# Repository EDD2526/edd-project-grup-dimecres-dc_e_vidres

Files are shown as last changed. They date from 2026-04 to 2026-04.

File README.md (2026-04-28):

View this project on [CADLAB.io](https://cadlab.io/project/30192). 

# Projecte ALÇA-VIDRES

>**Autors:** Àlex Requena , Alfred Abanto
>**Versió:** v3.2

----------

## Objectiu

>PCB per controlar les portes d'un cotxe.
Control de finestres
Controls de seguretat en finestres
Sistema de tancament i obertura de portes
Obertura de portes amb un lector RFID

## Diagrama de blocs
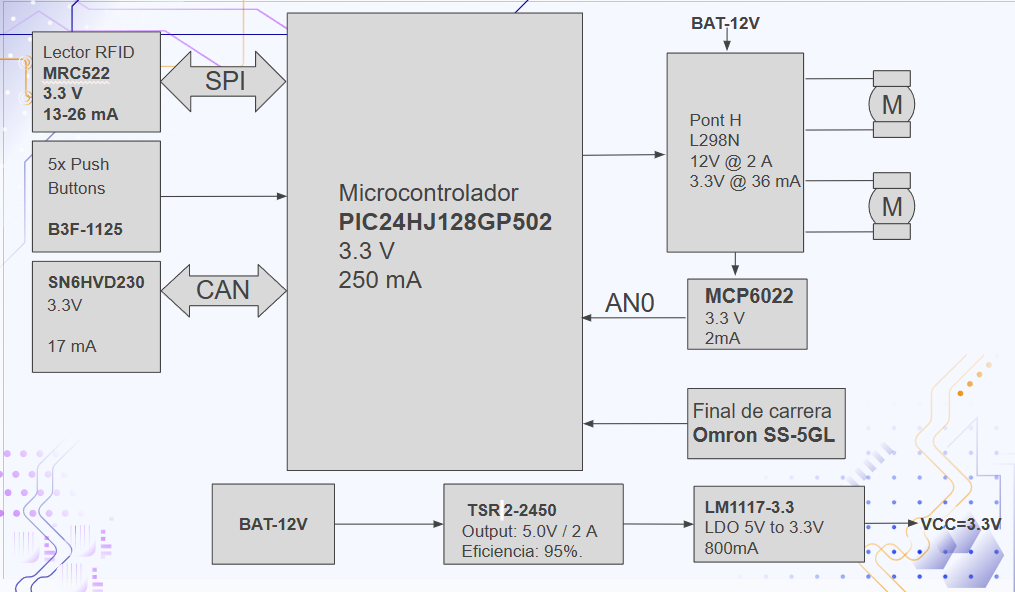
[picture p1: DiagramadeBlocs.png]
DIAGRAMA


### Descripció/funcionalitat de cada bloc
Microcontrolador PIC24HJ: Cervell del sistema; processa dades i coordina tots els mòduls i comunicacions.

Lector RFID MFRC522: Mòdul de comunicació sense contacte per a identificació de targetes via interfície SPI.

Polsadors B3F: Interfície d'usuari per a l'activació manual de funcions del sistema.

Transceptor CAN TJA1051: Interfície de comunicació robusta per a l'enviament de dades a llarga distància.

Pont H L298N: Driver de potència per controlar el gir i la velocitat de dos motors DC.

Amp. Op. MCP6022: Condiciona senyals analògics (com el consum dels motors) per a una lectura precisa del micro.

Final de carrera SS-01GL111-ET: Sensor mecànic de seguretat que detecta el límit de moviment físic.

Conversor TSR 2-2450: Transforma eficientment els 12V de la bateria en 5V estables.

Regulador LM1117-3.3: Redueix els 5V a 3.3V per alimentar la lògica i els xips de control.
## Requisits / Especificacions

----

## Components

| Descripci&#243; | Ref | Package |Datasheet | Prove&#239;dor | Preu | Unitats |
| Driver de Motor (Puente H) | L298N | TO-220-15 | [Datasheet](https://www.alldatasheet.com/datasheet-pdf/view/22440/STMICROELECTRONICS/L298N.html) | [Mouser](https://www.mouser.es/c/?q=L298N) | 10.31 &euro; | 1x |

| Convertidor DC-DC | TSR2-2450 | SIP-3 | https://www.tracopower.com/products/tsr2.pdf | https://www.mouser.es/c/?q=TSR2-2450 | 10.41 € | 1x |

| Amplificador Op. | MCP6022 | SOIC-8 | [Datasheet](https://www.alldatasheet.com/datasheet-pdf/view/99099/MICROCHIP/MCP6022.html) | [Mouser](https://www.mouser.es/c/?q=MCP6022) | 1.53 &euro; | 1x |
-----------
| Regulador LDO | LM1117DT-3.3 | TO-252 | https://www.ti.com/lit/ds/symlink/lm1117.pdf | https://www.mouser.es/c/?q=LM1117DT-3.3 | 1.5 € | 1x |
| Lector RFID | MFRC52201HN1_157 | HVQFN-32 | https://www.nxp.com/docs/en/data-sheet/MFRC522.pdf | https://www.mouser.es/c/?q=MFRC52201HN1_157 | 6.8€ | 1x |

| Microcontrolador | PIC24HJ64GP504-I/PT | TQFP-44 | https://ww1.microchip.com/downloads/en/DeviceDoc/70293G.pdf | https://www.mouser.es/c/?q=PIC24HJ64GP504-I/PT | 5.75 € | 1x |

| Transceptor CAN | SN65HVD230 | SOIC-8 | https://www.ti.com/lit/ds/symlink/sn65hvd230.pdf | https://www.mouser.es/c/?q=SN65HVD230 | 1.91 € | 1x |

| Ferrita | FerriteBead | SMD 0805 | https://www.vishay.com/docs/34025/ilbb0805.pdf| [Mouser](https://www.mouser.es/c/?q=Ferrite%20Bead%200805) | 0.08 &euro; | 1x |

| Conector D-Sub 9 | A-DF 09 LL/Z | THT | https://www.assmann-wsw.com/fileadmin/datasheets/ASS_0212_CO.pdf | https://www.mouser.es/c/?q=A-DF+09+LL%2FZ | 2.18 € | 2x |
## Software
Kicad
### Eines:

  * KiCad 10.0 

### Funcionalitats:
Controlar finestres.

Controls de seguretat en finestres.

Sistema de tancament i obertura de portes.

Obrir portes amb un lector RFID.

-----------

## Historial de canvis
|11/03| Alfred | Main | v0.0 | Diagrama de blocs i 
components |
|18/03| Àlex | Main | v0.1 | Esquemàtic i simulacions |
| 25/03| Àlex | Main | v1 | layoutv1|
| 10/04| Alfred | Main | v2 | layoutv2, dues etapes|
| 10/04| Alfred | Main | v3.0 | layoutv2, redistribució|
| 22/04| Àlex | Main | v3.1 | layoutv3, errors arreglats|
| 27/04| Àlex i Alfred | Main | v3.2| layoutv3, layout final|

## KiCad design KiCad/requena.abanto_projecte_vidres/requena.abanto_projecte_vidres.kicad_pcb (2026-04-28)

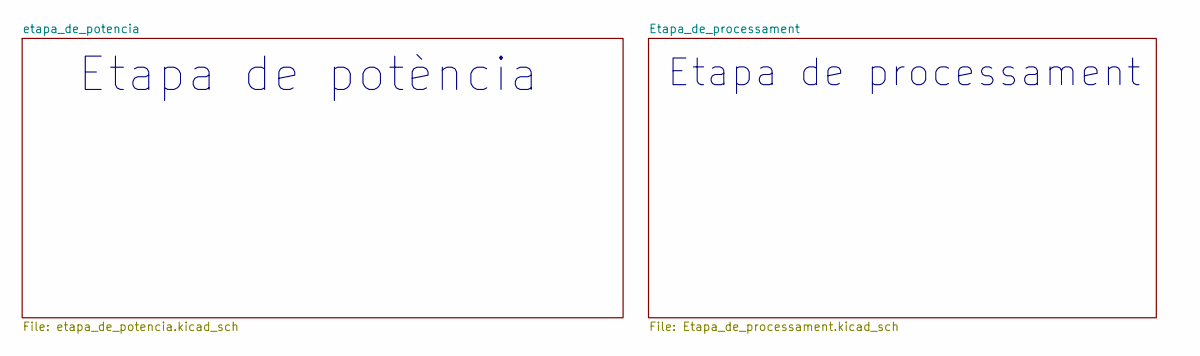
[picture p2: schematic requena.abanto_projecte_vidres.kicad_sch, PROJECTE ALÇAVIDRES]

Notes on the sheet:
Etapa de processament
Etapa de potència

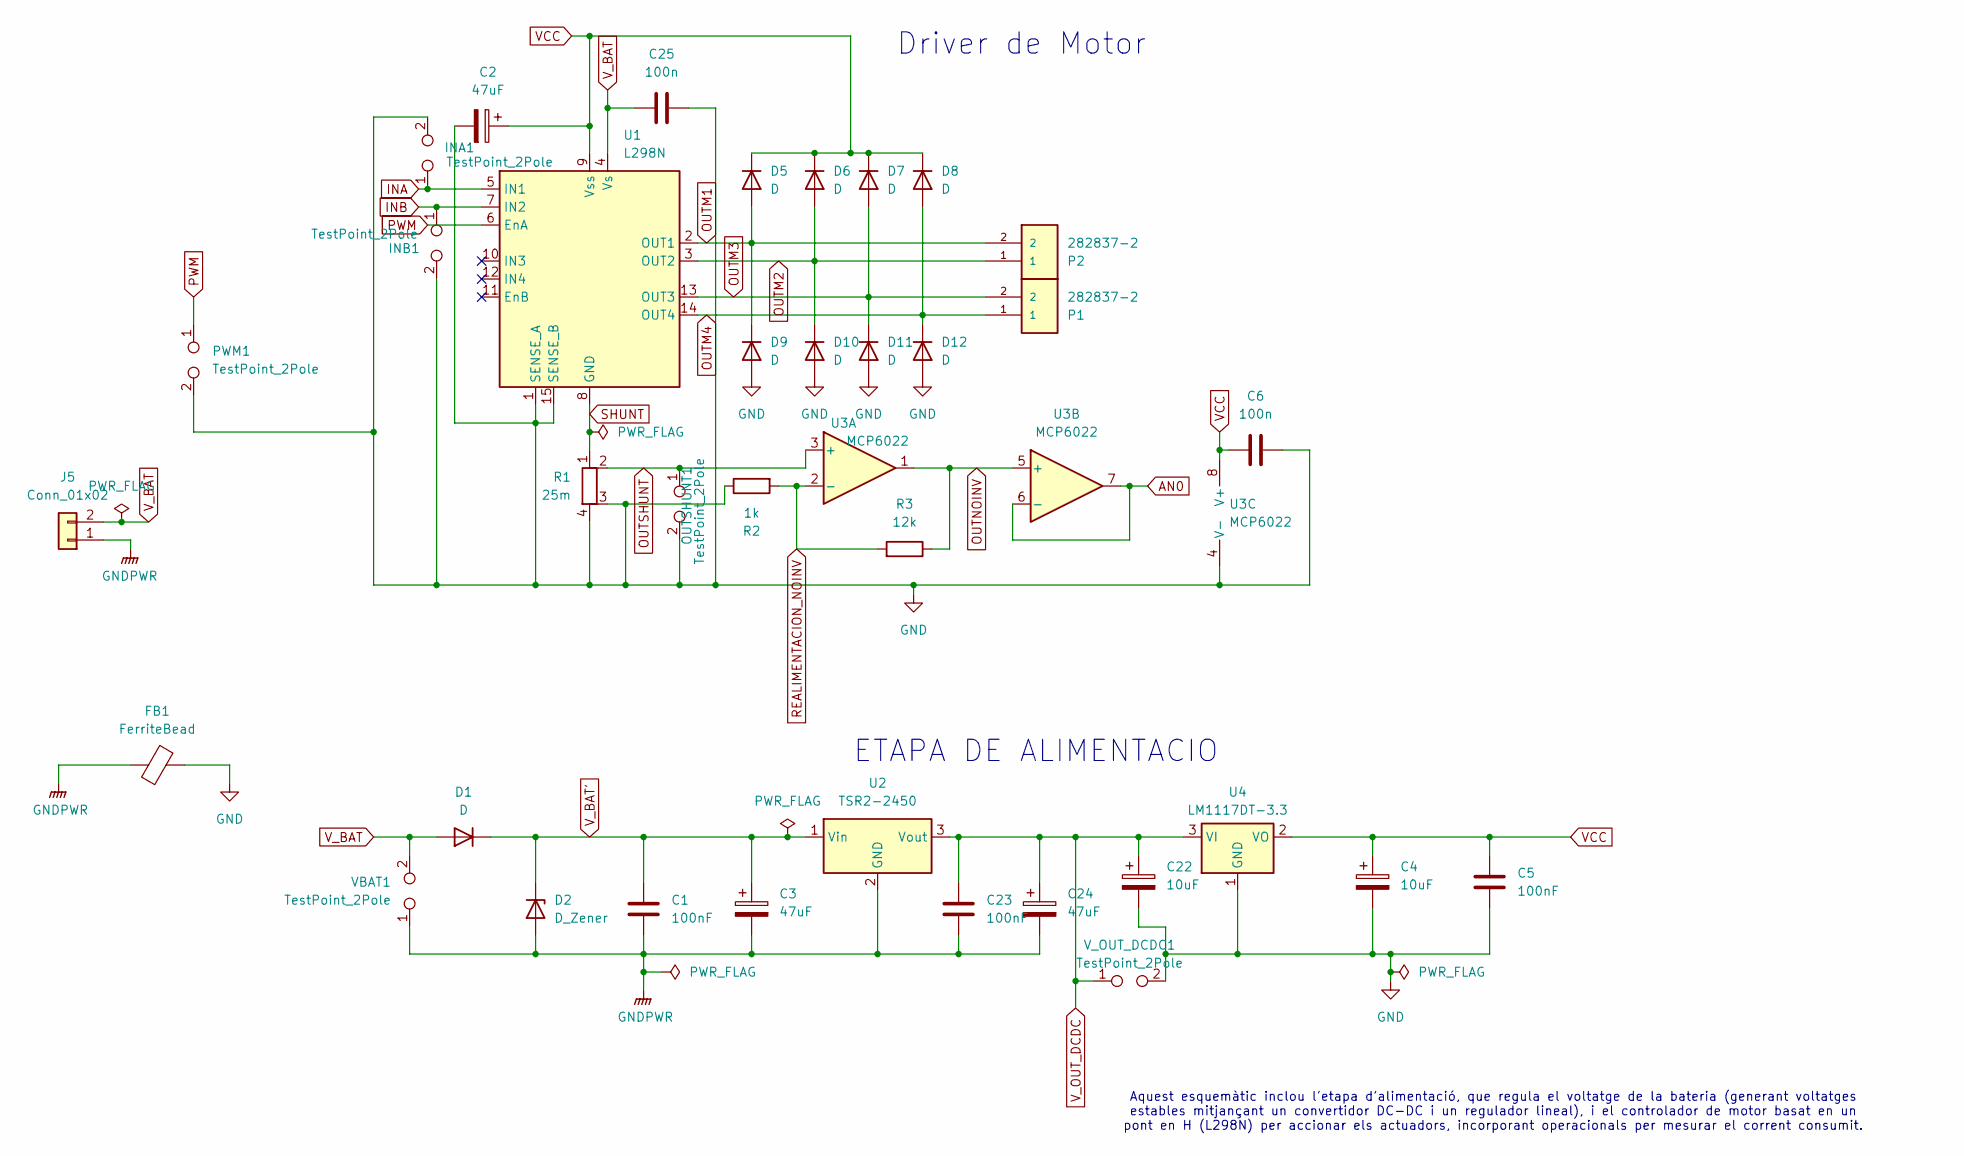
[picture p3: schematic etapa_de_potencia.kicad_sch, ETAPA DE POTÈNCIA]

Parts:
C1, C5, C23: 100nF; C_0805_2012Metric
C2, C3, C24: 47uF; CP_Radial_D4.0mm_P1.50mm
C4, C22: 10uF; CP_Radial_D4.0mm_P1.50mm
C6, C25: 100n; C_0603_1608Metric
D1: D; D_DO-41_SOD81_P12.70mm_Horizontal
D2: D_Zener; D_A-405_P2.54mm_Vertical_AnodeUp
D5, D6, D7, D8, D9, D10, D11, D12: D; D_DO-201AD_P15.24mm_Horizontal
FB1: FerriteBead; L_0805_2012Metric
INA1: TestPoint_2Pole; TestPoint_2Pads_Pitch2.54mm_Drill0.8mm
INB1: TestPoint_2Pole; TestPoint_2Pads_Pitch2.54mm_Drill0.8mm
J5: Conn_01x02; TerminalBlock_Xinya_XY308-2.54-2P_1x02_P2.54mm_Horizontal
OUTSHUNT1: TestPoint_2Pole; TestPoint_2Pads_Pitch2.54mm_Drill0.8mm
P1, P2: 282837-2; TE_282837-2; PARTREV G3
PWM1: TestPoint_2Pole; TestPoint_2Pads_Pitch2.54mm_Drill0.8mm
R1: 25m; R_Shunt_Vishay_WSK2512_6332Metric_T1.19mm
R2: 1k; R_1206_3216Metric
R3: 12k; R_1206_3216Metric
U1: L298N; TO-220-15_P2.54x5.08mm_StaggerOdd_Lead4.58mm_Vertical
U2: TSR2-2450; Converter_DCDC_TRACO_TSR2-xxxx_THT
U3: MCP6022; SOIC-8_3.9x4.9mm_P1.27mm
U4: LM1117DT-3.3; TO-252-2
VBAT1: TestPoint_2Pole; TestPoint_2Pads_Pitch2.54mm_Drill0.8mm
V_OUT_DCDC1: TestPoint_2Pole; TestPoint_2Pads_Pitch2.54mm_Drill0.8mm

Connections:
AN0: U3.6 (-), U3.7; also elsewhere on the board
GNDPWR: C1.2, C3.2, C23.2, C24.2, D2.2 (A), FB1.1, J5.1, U2.2 (GND), VBAT1.1
INA: INA1.1, U1.5 (IN1); also elsewhere on the board
INB: INB1.1, U1.7 (IN2); also elsewhere on the board
OUTM1: D5.2 (A), D9.1 (K), P2.2, U1.2 (OUT1)
OUTM2: D6.2 (A), D10.1 (K), P2.1, U1.3 (OUT2)
OUTM3: D7.2 (A), D11.1 (K), P1.2, U1.13 (OUT3)
OUTM4: D8.2 (A), D12.1 (K), P1.1, U1.14 (OUT4)
OUTNOINV: R3.1, U3.1, U3.5 (+)
OUTSHUNT: OUTSHUNT1.1, R1.2, U3.3 (+)
PWM: PWM1.1, U1.6 (EnA); also elsewhere on the board
REALIMENTACION_NOINV: R2.2, R3.2, U3.2 (-)
SHUNT: R1.1, U1.8 (GND)
VCC: C2.1, C4.1, C5.1, C6.1, D5.1 (K), D6.1 (K), D7.1 (K), D8.1 (K), U1.9 (Vss), U3.8 (V+), U4.2 (VO); also elsewhere on the board
V_BAT: C25.1, D1.2 (A), J5.2, U1.4 (Vs), VBAT1.2
V_BAT': C1.1, C3.1, D1.1 (K), D2.1 (K), U2.1 (Vin)
V_OUT_DCDC: C22.1, C23.1, C24.1, U2.3 (Vout), U4.3 (VI), V_OUT_DCDC1.1

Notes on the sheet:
Aquest esquemàtic inclou l'etapa d'alimentació, que regula el voltatge de la bateria (generant voltatges estables mitjançant un convertidor DC-DC i un regulador lineal), i el controlador de motor basat en un pont en H (L298N) per accionar els actuadors, incorporant operacionals per mesurar el corre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
Driver de Motor
ETAPA DE ALIMENTACIO

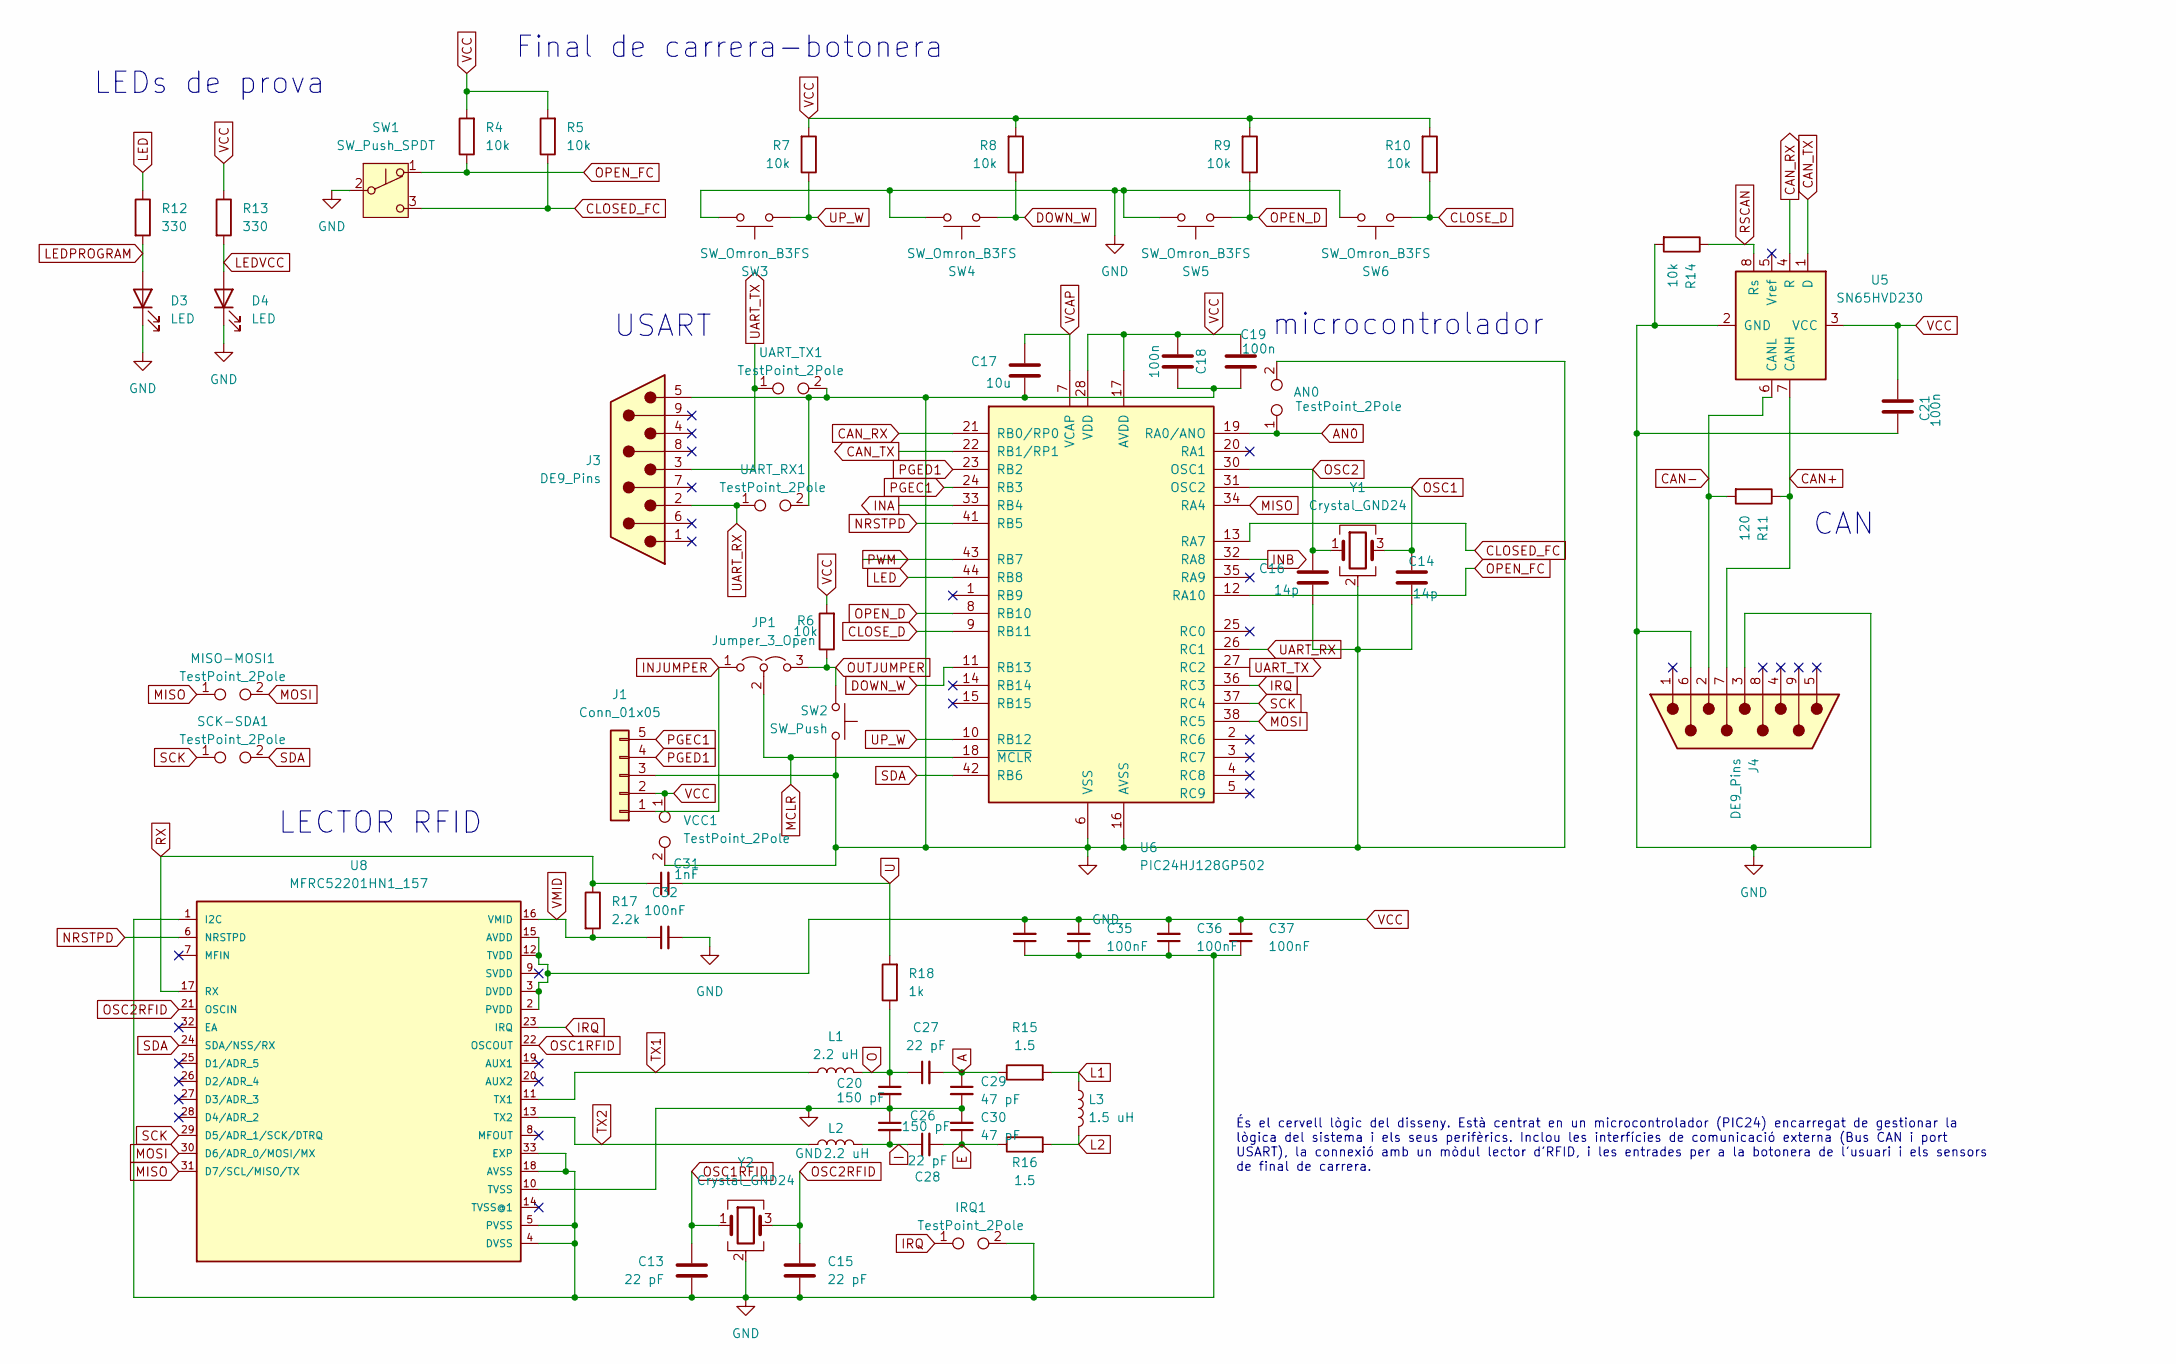
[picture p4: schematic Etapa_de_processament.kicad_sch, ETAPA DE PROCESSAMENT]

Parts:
AN0: TestPoint_2Pole; TestPoint_2Pads_Pitch2.54mm_Drill0.8mm
C13, C15: 22 pF; C_0805_2012Metric
C14, C16: 14p; C_0805_2012Metric
C17: 10u; C_0603_1608Metric
C18, C19, C21: 100n; C_0603_1608Metric
C20, C26: 150 pF; C_1206_3216Metric
C27, C28: 22 pF; C_1206_3216Metric
C29, C30: 47 pF; C_1206_3216Metric
C31: 1nF; C_1206_3216Metric
C32: 100nF; C_1206_3216Metric
C34, C35, C36, C37: 100nF; C_0603_1608Metric
D3, D4: LED; D_0805_2012Metric
IRQ1: TestPoint_2Pole; TestPoint_2Pads_Pitch2.54mm_Drill0.8mm
J1: Conn_01x05; PinHeader_1x05_P2.54mm_Vertical
J3, J4: DE9_Pins; DSUB-9_Pins_Horizontal_P2.77x2.54mm_EdgePinOffset9.40mm
JP1: Jumper_3_Open; PinHeader_1x03_P2.54mm_Vertical
L1, L2: 2.2 uH; L_1206_3216Metric
L3: 1.5 uH; L_1206_3216Metric
MISO-MOSI1: TestPoint_2Pole; TestPoint_2Pads_Pitch2.54mm_Drill0.8mm
R4, R5, R6, R7, R8, R9, R10, R14: 10k; R_1206_3216Metric
R11: 120; R_1206_3216Metric
R12, R13: 330; R_1206_3216Metric
R15, R16: 1.5; R_1206_3216Metric
R17: 2.2k; R_1206_3216Metric
R18: 1k; R_1206_3216Metric
SCK-SDA1: TestPoint_2Pole; TestPoint_2Pads_Pitch2.54mm_Drill0.8mm
SW1: SW_Push_SPDT; SW_SPDT_PCM12
SW2: SW_Push; SW_SPST_Omron_B3FS-100xP
SW3, SW4, SW5, SW6: SW_Omron_B3FS; SW_SPST_Omron_B3FS-100xP
U5: SN65HVD230; SOIC-8_3.9x4.9mm_P1.27mm
U6: PIC24HJ128GP502; TQFP-44_10x10mm_P0.8mm
U8: MFRC52201HN1_157; QFN50P500X500X100-33N
UART_RX1: TestPoint_2Pole; TestPoint_2Pads_Pitch2.54mm_Drill0.8mm
UART_TX1: TestPoint_2Pole; TestPoint_2Pads_Pitch2.54mm_Drill0.8mm
VCC1: TestPoint_2Pole; TestPoint_2Pads_Pitch2.54mm_Drill0.8mm
Y1: Crystal_GND24; Crystal_SMD_3225-4Pin_3.2x2.5mm
Y2: Crystal_GND24; Crystal_SMD_2520-4Pin_2.5x2.0mm

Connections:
A: C27.2, C29.1, R15.1
AN0: AN0.1, U6.19 (RA0/ANO); also elsewhere on the board
CAN+: J4.7, R11.1, U5.7 (CANH)
CAN-: J4.2, R11.2, U5.6 (CANL)
CAN_RX: U5.4 (R), U6.21 (RB0/RP0)
CAN_TX: U5.1 (D), U6.22 (RB1/RP1)
CLOSED_FC: R5.1, SW1.3 (C), U6.13 (RA7)
CLOSE_D: R10.1, U6.9 (RB11); also elsewhere on the board
DOWN_W: R8.1, U6.11 (RB13); also elsewhere on the board
E: C28.2, C30.1, R16.1
I: C26.2, C28.1, L2.2
INA: U6.33 (RB4); also elsewhere on the board
INB: U6.32 (RA8); also elsewhere on the board
INJUMPER: J1.1, JP1.1 (A)
IRQ: IRQ1.1, U6.36 (RC3), U8.23 (IRQ)
L1: L3.1, R15.2
L2: L3.2, R16.2
LED: R12.1, U6.44 (RB8)
LEDPROGRAM: D3.2 (A), R12.2
LEDVCC: D4.2 (A), R13.2
MCLR: JP1.2 (C), U6.18 (~MCLR)
MISO: MISO-MOSI1.1, U6.34 (RA4), U8.31 (D7/SCL/MISO/TX)
MOSI: MISO-MOSI1.2, U6.38 (RC5), U8.30 (D6/ADR_0/MOSI/MX)
NRSTPD: U6.41 (RB5), U8.6 (NRSTPD)
O: C20.1, C27.1, L1.2, R18.1
OPEN_D: R9.1, U6.8 (RB10); also elsewhere on the board
OSC1: C14.1, U6.31 (OSC2), Y1.3
OSC1RFID: C13.1, U8.22 (OSCOUT), Y2.1
OSC2: C16.1, U6.30 (OSC1), Y1.1
OSC2RFID: C15.1, U8.21 (OSCIN), Y2.3
OUTJUMPER: JP1.3 (B), R6.1; also elsewhere on the board
PGEC1: J1.5, U6.24 (RB3)
PGED1: J1.4, U6.23 (RB2)
PWM: U6.43 (RB7); also elsewhere on the board
RSCAN: R14.1, U5.8 (Rs)
RX: C31.1, R17.1, U8.17 (RX)
SCK: SCK-SDA1.1, U6.37 (RC4), U8.29 (D5/ADR_1/SCK/DTRQ)
SDA: SCK-SDA1.2, U6.42 (RB6), U8.24 (SDA/NSS/RX)
TX1: L1.1, U8.11 (TX1)
TX2: L2.1, U8.13 (TX2)
U: C31.2, R18.2
UART_RX: J3.2, U6.26 (RC1), UART_RX1.1
UART_TX: J3.3, U6.27 (RC2), UART_TX1.1
VCAP: C17.1, U6.7 (VCAP)
VCC: C18.2, C19.1, C21.1, C34.2, C35.2, C36.2, C37.2, J1.2, R4.2, R5.2, R6.2, R7.2, R8.2, R9.2, R10.2, R13.1, U5.3 (VCC), U6.17 (AVDD), U6.28 (VDD), U6.40 (VDD), U8.2 (PVDD), U8.3 (DVDD), U8.12 (TVDD), U8.15 (AVDD), VCC1.1; also elsewhere on the board
VMID: C32.1, R17.2, U8.16 (VMID)

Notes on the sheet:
CAN
LEDs de prova
LECTOR RFID
microcontrolador
USART
Final de carrera-botonera
És el cervell lògic del disseny. Està centrat en un microcontrolador (PIC24) encarregat de gestionar la lògica del sistema i els seus perifèrics. Inclou les interfícies de comunicació externa (Bus CAN i port USART), la connexió amb un mòdul lector d'RFID, i les entrades per a la botonera de l'usuar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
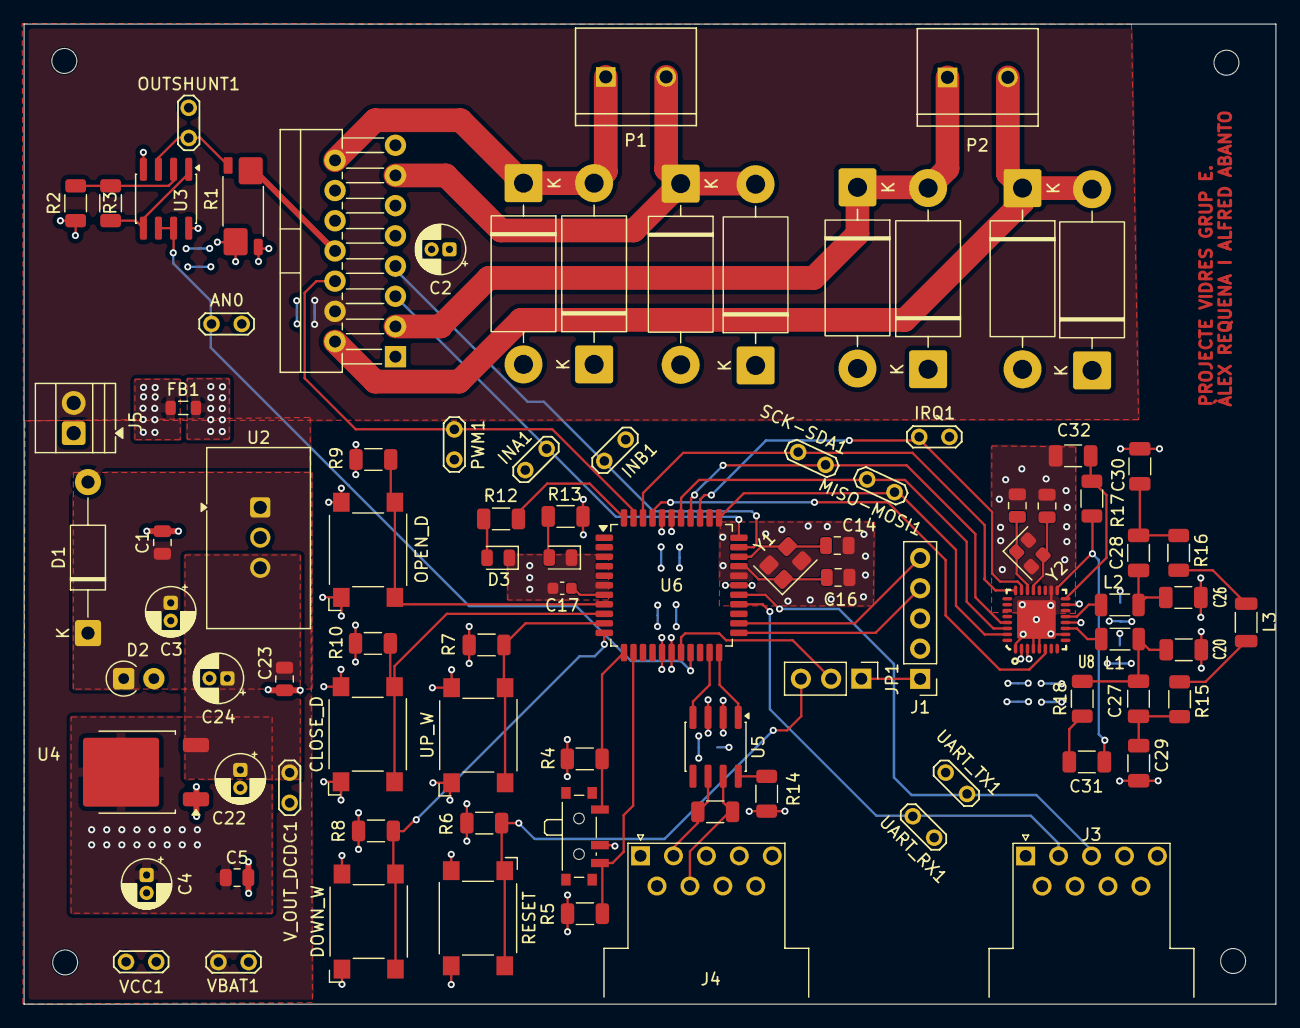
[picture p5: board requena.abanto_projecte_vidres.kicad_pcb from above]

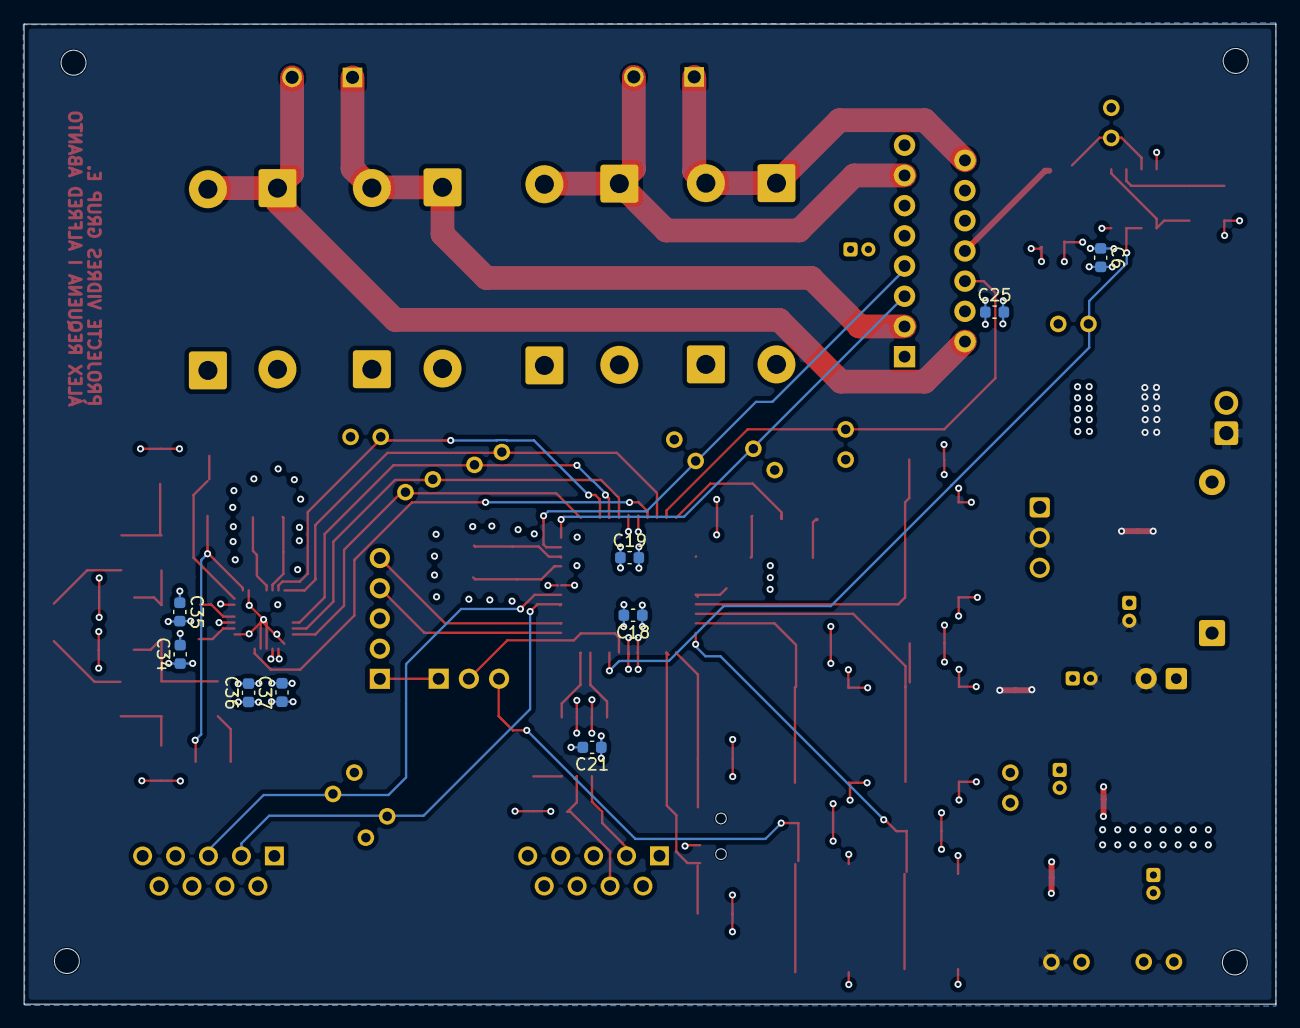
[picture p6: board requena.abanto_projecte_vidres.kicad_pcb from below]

Board: 4 copper layers, 105.3 x 82.4 mm, 99 parts (9 on the bottom side), 61 nets.

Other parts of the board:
CLOSE_D: SW_Omron_B3FS; SW_SPST_Omron_B3FS-100xP
DOWN_W: SW_Omron_B3FS; SW_SPST_Omron_B3FS-100xP
OPEN_D: SW_Omron_B3FS; SW_SPST_Omron_B3FS-100xP
RESET: SW_Push; SW_SPST_Omron_B3FS-100xP
UP_W: SW_Omron_B3FS; SW_SPST_Omron_B3FS-100xP

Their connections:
CLOSE_D: CLOSE_D.2; also elsewhere on the board
DOWN_W: DOWN_W.2; also elsewhere on the board
OPEN_D: OPEN_D.2; also elsewhere on the board
OUTJUMPER: RESET.1; also elsewhere on the board

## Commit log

2026-03-11 creacion proyecto kikad
    [requena.abanto_projecte_vidres.kicad_pcb, requena.abanto_projecte_vidres.kicad_sch]
2026-03-12 Creacio d'etapes
    [Etapa_de_alimentacio.kicad_sch, Etapa_de_comunicacio.kicad_sch, Etapa_de_processament.kicad_sch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]
2026-03-14 etapa alimentación empezada
    [Etapa_de_alimentacio.kicad_sch]
2026-03-15 avance can
    [Etapa_de_comunicacio.kicad_sch]
2026-03-15 avance etapa-de-processament
    [Etapa_de_processament.kicad_sch]
2026-03-15 He ficar un led
    [Etapa_de_processament.kicad_sch]
2026-03-15 avance comunicaciones
    [Etapa_de_comunicacio.kicad_sch]
2026-03-15 posar etiquetes
    [Etapa_de_processament.kicad_sch]
2026-03-15 millora circuit
    [Etapa_de_processament.kicad_sch]
2026-03-15 proteccion alimentacion
    [Etapa_de_alimentacio.kicad_sch]
2026-03-15 avance sensores
    [Etapa_de_sensors.kicad_sch]
2026-03-15 avance etapa de potencia
    [etapa_de_potencia.kicad_sch]
2026-03-16 cambios de clase
    [Etapa_de_processament.kicad_sch, Etapa_de_sensors.kicad_sch]
2026-03-16 arreglos :)
    [Etapa_de_comunicacio.kicad_sch]
2026-03-17 millora el esquematic
    [Etapa_de_comunicacio.kicad_sch, Etapa_de_processament.kicad_sch, Etapa_de_sensors.kicad_sch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]
2026-03-22 Millora projecte 1
    [Etapa_de_alimentacio.kicad_sch, Etapa_de_comunicacio.kicad_sch, Etapa_de_processament.kicad_sch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]
2026-03-24 milora_esquema_i_layoutcomençat
    [Etapa_de_processament.kicad_sch, etapa_de_potencia.kicad_sch, requena.abanto_projecte_vidres.kicad_pcb]
2026-04-05 Millora del micro a 44 pins
    [Etapa_de_processament.kicad_sch]
2026-04-05 esquema acabat
    [Etapa_de_processament.kicad_sch, etapa_de_potencia.kicad_sch, requena.abanto_projecte_vidres.kicad_pcb]
2026-04-05 a mimir
    [Etapa_de_processament.kicad_sch, requena.abanto_projecte_vidres.kicad_pcb]
2026-04-06 primera pcb
    [Etapa_de_processament.kicad_sch, etapa_de_potencia.kicad_sch, requena.abanto_projecte_vidres.kicad_pcb]
2026-04-06 Avenç de placement
    [Etapa_de_processament.kicad_sch, etapa_de_potencia.kicad_sch, requena.abanto_projecte_vidres.kicad_pcb]
2026-04-06 alfred guapo
    [Etapa_de_processament.kicad_sch, requena.abanto_projecte_vidres.kicad_pcb]
2026-04-08 placement pcb
    [etapa_de_potencia.kicad_sch, requena.abanto_projecte_vidres.kicad_pcb]
2026-04-09 ficat diodes de proteccion driver
    [etapa_de_potencia.kicad_sch, requena.abanto_projecte_vidres.kicad_pcb]
2026-04-09 foking diodos
    [etapa_de_potencia.kicad_sch, requena.abanto_projecte_vidres.kicad_pcb]
2026-04-09 buenas noches alfred
    [Etapa_de_processament.kicad_sch, etapa_de_potencia.kicad_sch, requena.abanto_projecte_vidres.kicad_pcb]
2026-04-10 Placement més o menys colocat, i avenç de algunes connexions
    [Etapa_de_processament.kicad_sch, requena.abanto_projecte_vidres.kicad_pcb]
2026-04-11 el RFID me jodio la vida
    [Etapa_de_processament.kicad_sch, requena.abanto_projecte_vidres.kicad_pcb]
2026-04-11 viva el peru
    [requena.abanto_projecte_vidres.kicad_pcb]
2026-04-12 hamza zibar
    [requena.abanto_projecte_vidres.kicad_pcb]
2026-04-15 regles de disseny i més coses
    [Etapa_de_processament.kicad_sch, etapa_de_potencia.kicad_sch, requena.abanto_projecte_vidres.kicad_pcb]
2026-04-19 hola alfred
    [Etapa_de_processament.kicad_sch, etapa_de_potencia.kicad_sch, requena.abanto_projecte_vidres.kicad_pcb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]
2026-04-19 he posat una petjada i simbol
    [Etapa_de_processament.kicad_sch]
2026-04-19 bomboclat walahi
    [Etapa_de_processament.kicad_sch, requena.abanto_projecte_vidres.kicad_pcb]
2026-04-21 joan canals el mejor
    [requena.abanto_projecte_vidres.kicad_pcb]
2026-04-24 algunes millores
    [Etapa_de_processament.kicad_sch, etapa_de_potencia.kicad_sch, requena.abanto_projecte_vidres.kicad_pcb]
2026-04-25 faltan tests points
    [Etapa_de_processament.kicad_sch, etapa_de_potencia.kicad_sch, requena.abanto_projecte_vidres.kicad_pcb]
2026-04-25 alfred butanero
    [Etapa_de_processament.kicad_sch, etapa_de_potencia.kicad_sch, requena.abanto_projecte_vidres.kicad_pcb]
2026-04-26 huellas arregladas
    [Etapa_de_processament.kicad_sch, etapa_de_potencia.kicad_sch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]
2026-04-28 alfred masoquista
    [Etapa_de_processament.kicad_sch, etapa_de_potencia.kicad_sch, requena.abanto_projecte_vidres.kicad_pcb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]
